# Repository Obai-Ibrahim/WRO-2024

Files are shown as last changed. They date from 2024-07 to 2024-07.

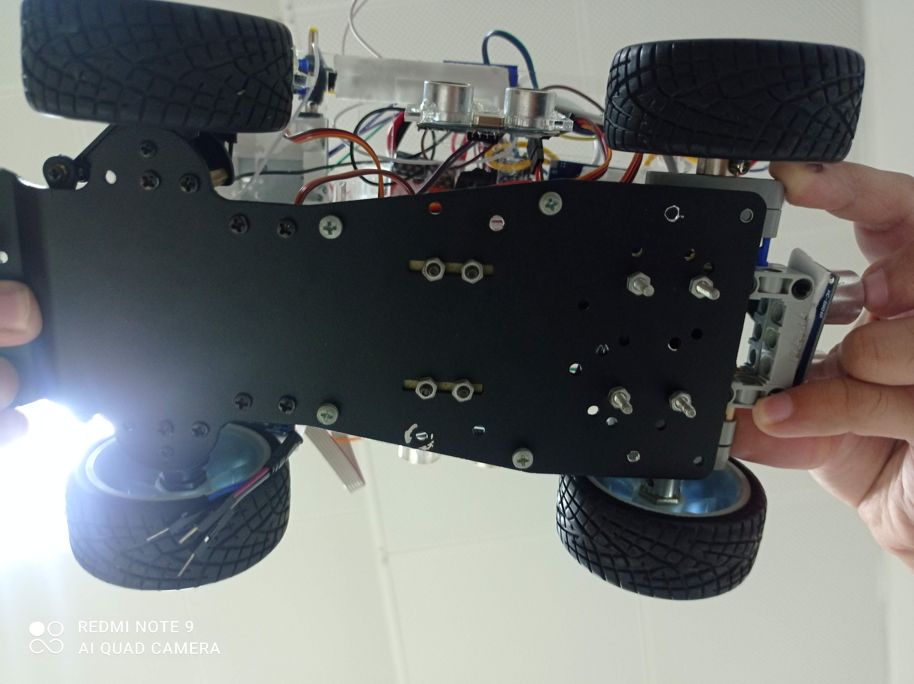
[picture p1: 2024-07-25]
Vehicle Pictures/Bottom.jpg

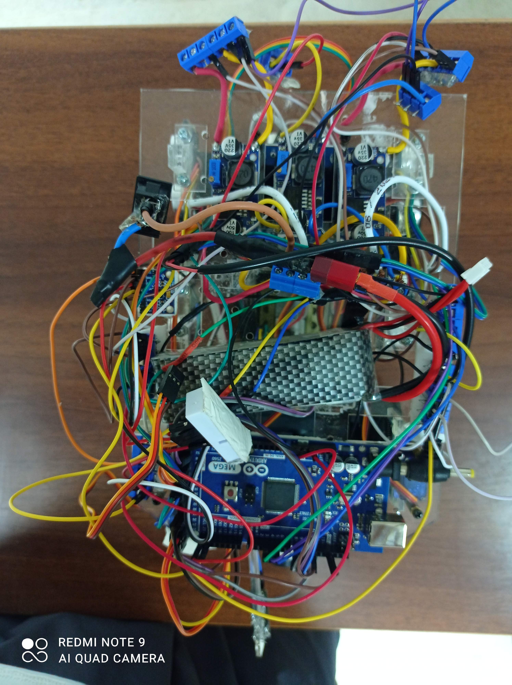
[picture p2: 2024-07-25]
Vehicle Pictures/Up.jpg

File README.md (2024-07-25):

## INTRODUCTION
This Repository contains all the necessary information to build a self-driving car, which can complete three laps and handle different configurations of obstacles.
The code is written with Arduino C programming language, which controls the motor's movement based on the different sensors reading and mainly the information from the pixy cam.
The Repository contains an explanation of many aspects like the strategies and the power and mobility management. In the directory (other) many files will declare the calculation and the algorithms in a better way.
These files are:
Diagrams, DC motor, Power consumption and power supply, Driver.

## Open challenge strategy
For the open challenge, our algorithm depends basically on the distance sensors (HC-SR04) and the IMU (MPU6050) sensor, we implemented a Kalman filter to get accurate measurements of the orientation.
There are 8 ultrasonic sensors postured as shown in (found in others directory).
* The front one is (0) and the back one is (4)
* (2) and  (3) are the right sensors used to detect the turn in the clockwise round.
* (2) and  (3) are the right sensors used to detect the turn in the clockwise round.
* (1)  And (7) are installed on two sgSG-90ervo motors which move according to the Robot’s angle to guarantee good measurement of the perpendicular distance from the walls.
As the new rule states that the vehicle must not touch the outer wall, we declared a dangerous area which is 8cm from the outer wall.
The robot moves forward controlling the direction with PDthe  controller based on MPthe U6050 reading.
## Obstacle challenge strategy
We found out that planning a path for each stretch of the map and guiding the robot to follow it can be a confusing method because it needs perfect calibration for our camera and this may take a long time (maybe preparation time before the round is not sufficient).
So the algorithm in the first turn (the pillars are not known yet) will be: 
The vehicle will pass the forward section in two stages and the corner section in one stage. In the forward section, the pixy will detect the pillars location and then path the pillars one by one (the flow chart in (the others directory will declare this better))

After the first round the pillars positions are known, so we will follow the second strategy:
 By knowing the current position, current heading, target position, and target heading we can generate a polynomial to fit these parameters. Using multiple target points, we create a target path for the robot to follow, steering it towards the next point. This path accounts for the position of obstacles, mapping points to avoid them. We repeat this process until all three rounds are completed.

Note: detailed diagrams for both open and obstacle challenges are included in the directory (others)

## Mobility management
Vehicle’s chassis:
We bought a simple chassis with Ackerman for front-wheel servo steering. The kit contained four wheels, one metal base, nuts and bolts, a DC Motor, and a servo motor with an Ackerman mechanism with no sensors or additional parts. After that, we chose a suitable set of sensors and power supplies. We planned in advance to use a multi-floor design with 3D printed Ultrasonic holders and laser cut floor to have a balanced weight distribution.  
We used another DC motor because the one with the kit was not good, also we changed the rear axle and assembled the wheels with a Lego differential to move better, especially on turns.
To do this we printed a 3D coupler to transfer movement from the engine to the differential’s axis.
The 3D printed parts and plexi laser cut parts are included in the directory (models).
Details of the motor and the torque calculation are in the directory (others).

## Power and sense management
The power calculations are detailed in a PDF file in the directory (scheme). The file contains an accurate calculation of the needed current and the needed supply voltage for the circuit components, in addition, some requirements were considered to choose a suitable battery to supply the sensors and actuators with sufficient power.
The used sensors are: 
1. ultrasonic sensors: dealing with walls and barriers can be enhanced with Ultrasonic Sensor. You shoot out a sound, wait to hear it echo back, and if you have your timing right, you will know how far away the wall is. Using the HC-SR04 Ultrasonic Sensor made it easy for our vehicle to avoid hitting the walls and find its best route between the colored pillars.

2. Gyroscope and accelerometer: We used MPU6050 to determine the vehicle’s rotation angle when it turns right or left. It also helps us to measure acceleration, velocity, orientation, displacement, and many other motion-related parameters of a system or object. This module also has a Digital Motion Processor inside it which is powerful enough to perform complex calculations and thus free up the work for Microcontroller. It has well documented and revised libraries available hence it’s very easy to use with famous platforms like Arduino.

3. TCRT5000Analog: helps to detect the turn if there is doubt with it as it can detect whether the color is white or nonotit is not used so much but can be useful in some cases, it is mounted with a servo motor to control its angle and to put it up when not used so it will not affect the camera readings.

4. Pixy2.1 camera: Using the second version of Pixy made the process smooth and fast with easy-to-detect errors and precise color detection. We faced many problems at the beginning as the camera could only deal with a small range of colors with almost perfect lighting conditions, but this problem was resolved by adjusting camera settings and calibrating it with more than one shade of each color. The information returned by the pixy are the detected objects with their coordinates and sizes.

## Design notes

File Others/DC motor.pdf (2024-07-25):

Torque calculations:

Each DC motor must be capable of generating a torque proportional to the load requirements of the mobile robot. The torque can be calculated using the following formula:

Ffriction = µ ∗ N | (1)

µ: coefficient of friction. N: normal force (Reaction).

N = m ∗ g | (2)

m: robot mass with payload. g: gravitational acceleration.

Facceleration = m ∗ a | (3)

a: robot acceleration.

The total force required for the robot to move:

Ftotal = Ffriction + Facceleration | (4)

T =

Ftotal ∗ r
k

(5)

k: number of DC motors (one motor in our case).

The nominal torque and velocity were

The minimum nominal torque is 8.5 kg. cm and the nominal velocity equals 245 rpm.

Our DC motor
The chosen motor is a 12 volts 350 RPM dc motor (with encoder) with the following specifications:
- Nominal Voltage: 12V
- Gear Reduction Ratio: 34:1
- No Load Speed: 350 rpm
- No Load Current: 20 mA
- Maximum efficiency point parameters: 2.0kg.cm/285rpm/5.0W/0.65A
- Maximum power point parameters: 5.8kg.cm/180rpm/9.0W/1.65A
- Stop current: 5.5A
- Stall torque: 12kg.cm
- Hall Resolution: 374
- Weight: 98g

We chose this dc motor because it has high torque and good speed control, we need this torque especially in starting the motion and in heavy turns as it needs high torque.

The torque helps to maintain a constant speed under in the existence of external loads so it is perfect for this application, also it has a good accurate encoder with 374 pulse per rotation which help to control the velocity and to measure the distance depending on wheel odometry.

Additionally, this motor can be easily controlled by a motor driver (which is BTS 7960 in our case), this make it suitable for robotics applications that requires precise motion.

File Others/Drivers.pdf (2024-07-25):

Drivers: BTS9670:

BTS7960 Motor Driver:

We used BTS7960 motor driver to control the speed and direction of the

DC motor. It is widely used with robotics, consumer electronics, automation

and other projects. It has very low voltage drop compared to other drivers

like L298N

Technical Specifications:

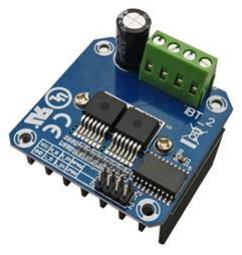
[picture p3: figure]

- Input Voltage: 6 – 27 V
- Driver: Dual BTS7960 H Bridge Configuration.
- Peak current: 43 A
- PWM capability of up to 25 kHz
- Control Input Level: 3.3 – 5V
- Control Mode: PWM or level
- Board Size (LxWxH): 50mm x 50mm x 43mm
- Weight: ~66g

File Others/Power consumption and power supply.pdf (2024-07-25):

Power consumption and power supply:

The following table contains each motor/sensor nominal current and supply (input) voltage:

Sensor/Motor/controller | Number of pieces | Nominal current(mA) | Total (mA) | Supply (input) voltage(volts)
Arduino mega | 1 | 74 | 74 | 8
BTS 7960 | 1 | 10 | 10 | 12(for motor) and 5 (for the inner controller)
Voltage regulator | 3 | 8 | 8 | 12
Pixy cam | 1 | 140 | 140 | 5
HC-SR04 sensor | 8 | 21 | 161 | 5
MPU6050 | 1 | 10 | 10 | 3.3
Motor Encoder | 1 | 2 | 2 | 5
TCRT5000 ANALOG | 1 | 7 | 7 | 5
MG995 servo motor | 1 | 350 | 350 | 5.8
SG-90 servo motor | 3 | 270 | 810 | 4.8
DC motor | 1 | 1650 | 1650 | 12 (BTS output)

The maximum needed input voltage is 12 volts
And the consumed current is 3.222 Amp if all the electronic components and actuator work simultaneously.

To choose our power supply we need to consider the following requirements:

- Stable current output
- High voltage under load
- Low temperature under high discharge
- Good capacity (can run the robot for 30 minutes at least)
- Low weight

To run the robot for 0.5 hour under a discharge of 3.2A we need minimum capacity of 1600 Ma Considering the previous requirements, we choose an 1800 11.1v 1.8Ah Li-Po battery.

Li-poly Battery:

We used one Li-poly battery to supply the Arduino board, sensors, DC and servo Motors and BTS.

Technical specifications:

Voltage: +11.1V

Capacity: 4200mAh

Number of cells: 3 cells

Weight: 315g

Size: 139mm x 43mm x 25mm

Plug: XT60 black

Charging connector: JST-XHR white

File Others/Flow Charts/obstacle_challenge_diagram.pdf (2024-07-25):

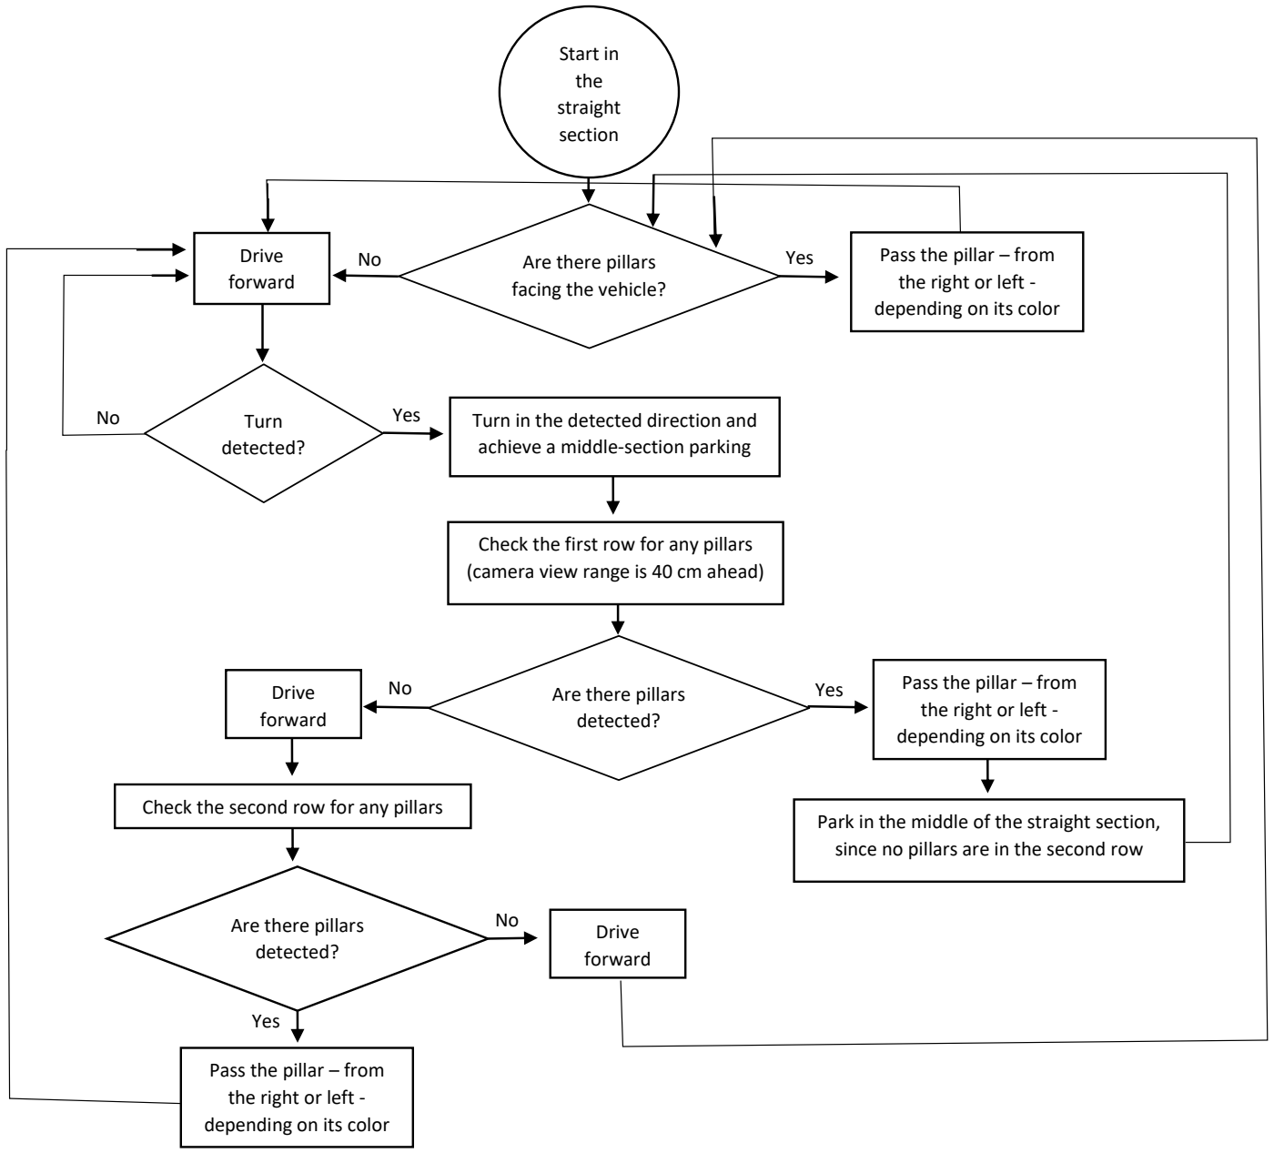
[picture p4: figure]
Start in the straight section; Are there pillars facing the vehicle?; Drive; Yes; forward; Turn detected?; achieve a middle-section parking; Pass the pillar – from the right or left - depending on its color; Check the first row for any pillars (camera view range is 40 cm ahead); Are there pillars detected?; Pass the pillar – from; the right or left - depending on its color; since no pillars are in the second row; Drive forward; Check the second row for any pillars

No | Yes | Turn in the detected direction and

Park in the middle of the straight section,

Note:

Regarding the parking lot, we considered passing next to it when it is not the final lap yet.

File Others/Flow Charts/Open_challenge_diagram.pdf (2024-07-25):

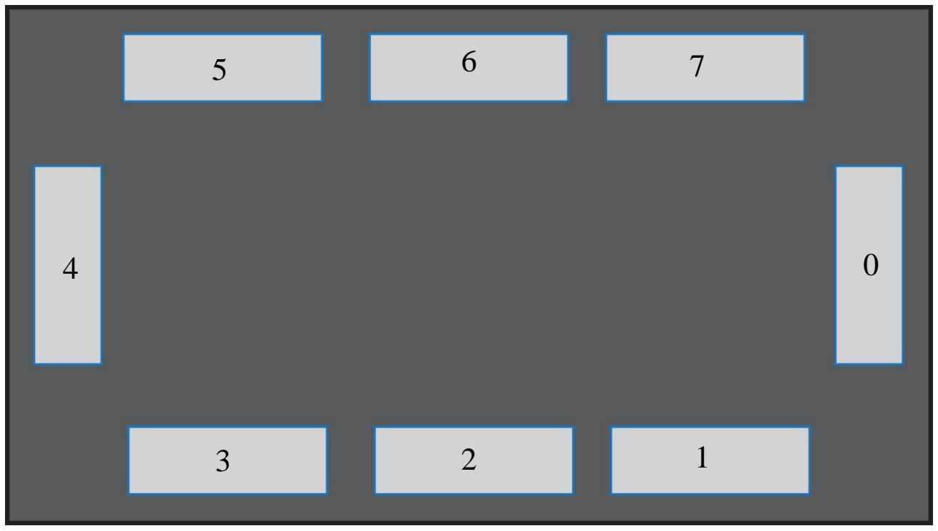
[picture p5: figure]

Sensor ID | Name | Sensor ID | Name
0 | Front | 4 | Back
1 | Right Servo | 5 | Back left
2 | Middle right | 6 | Middle left
3 | Back right | 7 | Left Servo

“Right Servo” and “Left Servo” are ultrasonic sensors put on two servomotors on the right and left respectively.

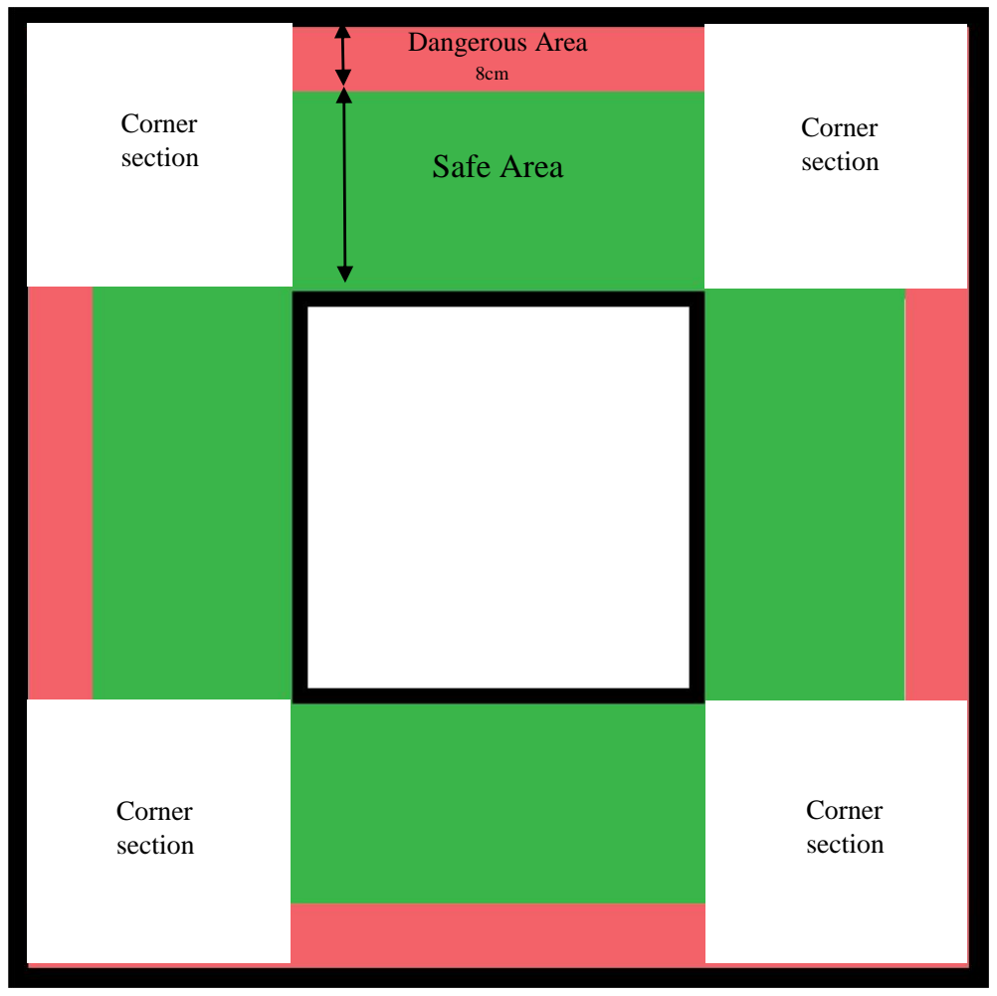
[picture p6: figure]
Safe Area; Dangerous Area; Corner section
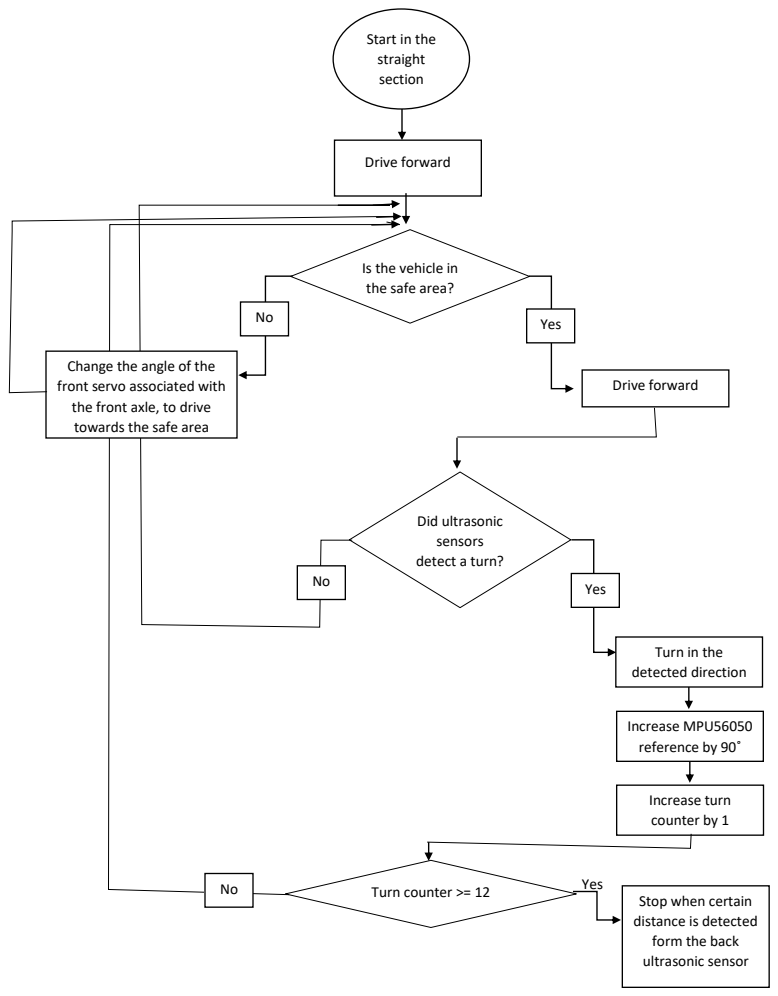
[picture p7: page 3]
Drive forward; Yes No; Did ultrasonic sensors detect a turn? Yes No; Increase MPU56050 reference by 90˚; Increase turn counter by 1; Turn counter >= 12; Yes

Start in the
straight
section

Is the vehicle in
the safe area?

Change the angle of the
front servo associated with
the front axle, to drive
towards the safe area

Turn in the
detected direction

Stop when certain
distance is detected
form the back
ultrasonic sensor

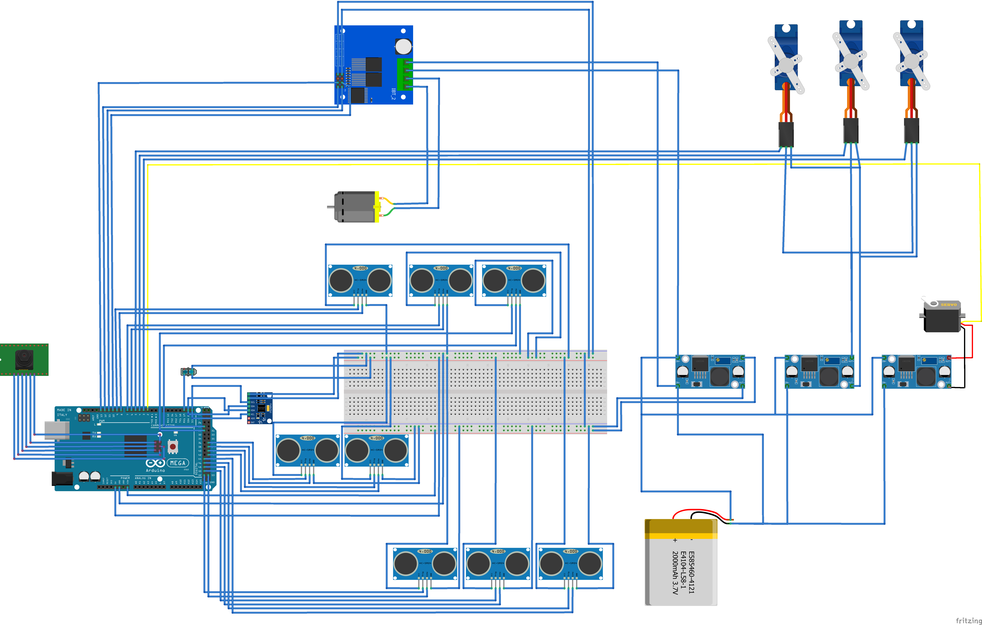
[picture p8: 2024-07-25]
Scheme/WRO_bb.png

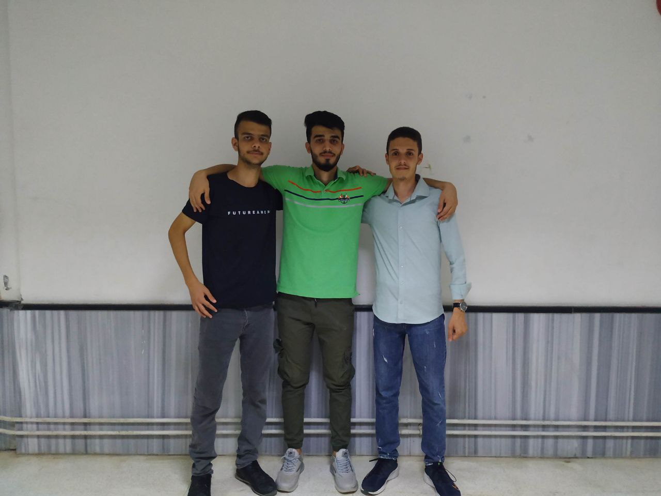
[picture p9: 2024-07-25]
Team Photos/Official.jpg

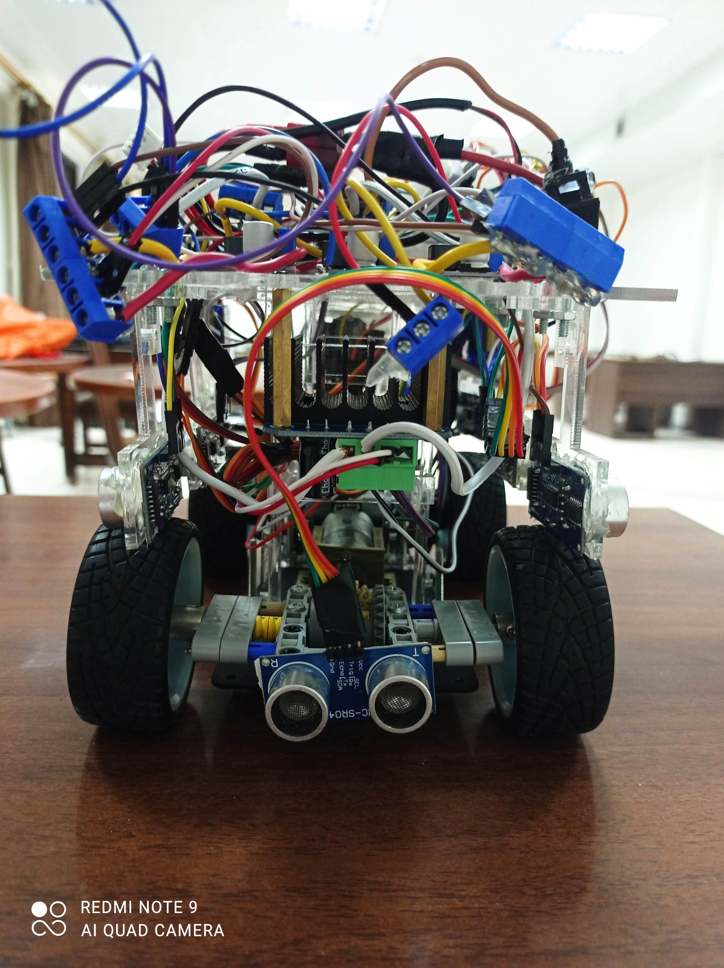
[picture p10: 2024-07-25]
Vehicle Pictures/Back.jpg

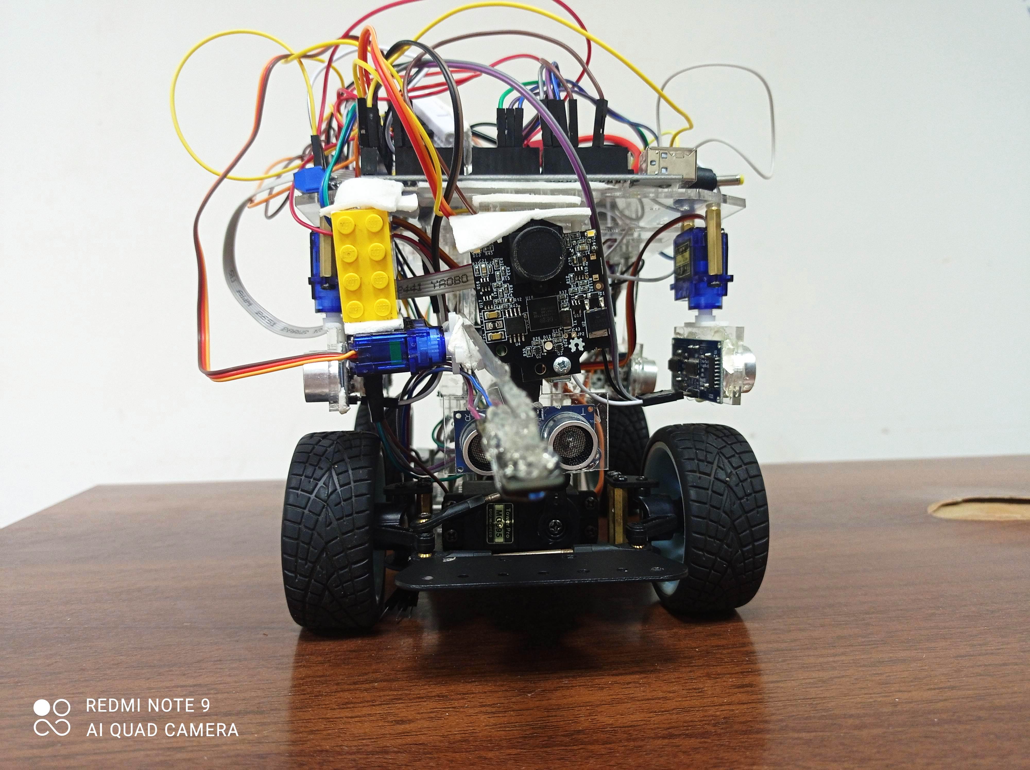
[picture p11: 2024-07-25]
Vehicle Pictures/Front.jpg

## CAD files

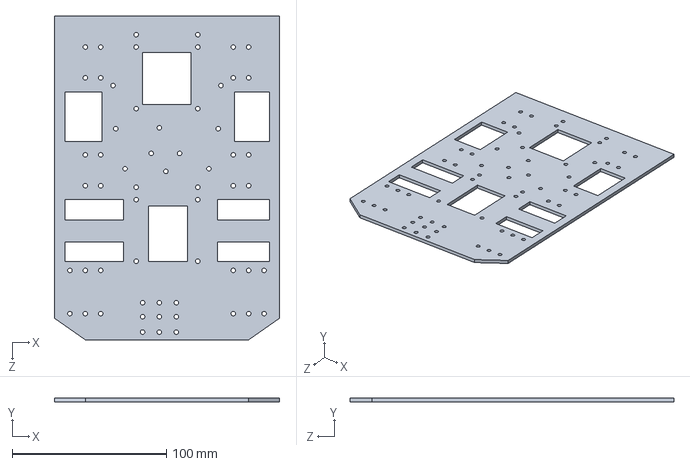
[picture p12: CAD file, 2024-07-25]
Model/Plexi/MAIN.SLDPRT
146.0 x 2.54 x 210.0 mm

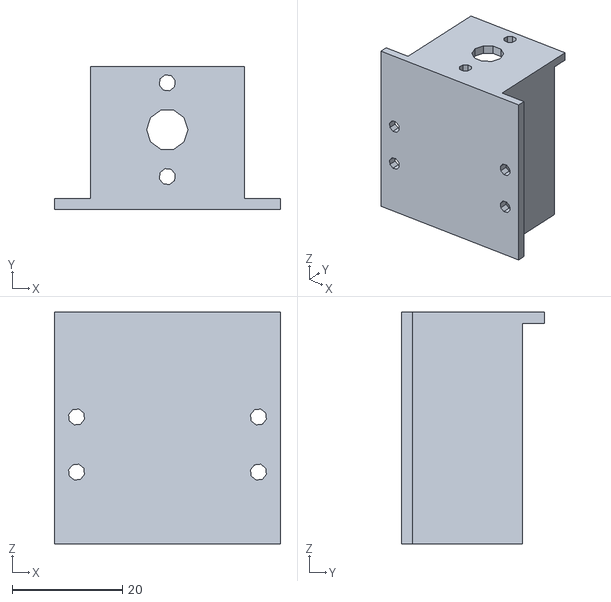
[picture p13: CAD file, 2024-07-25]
Model/3D Print/Dc_motor_holderstl.stl
41.0 x 26.0 x 42.0

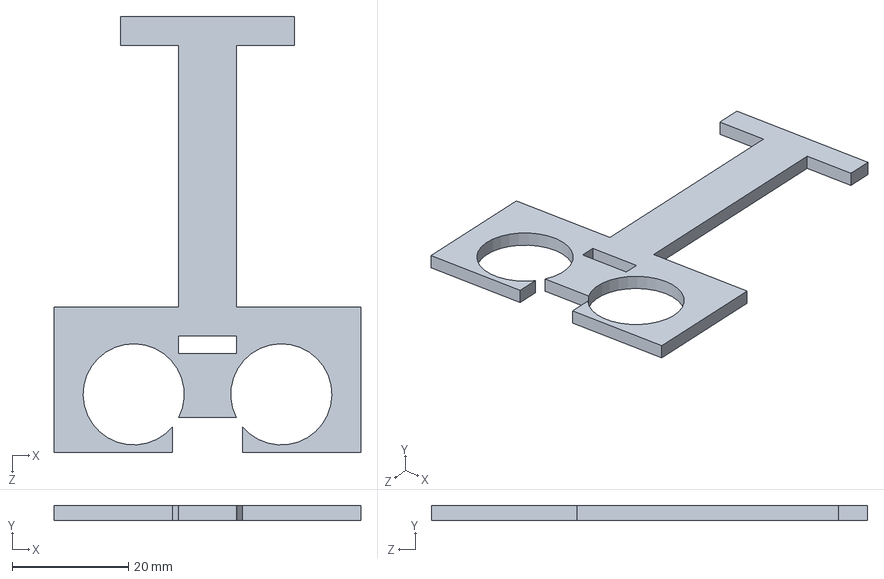
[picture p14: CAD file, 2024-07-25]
Model/Plexi/Ultrasonic holder.SLDPRT
52.8 x 2.54 x 75.0 mm

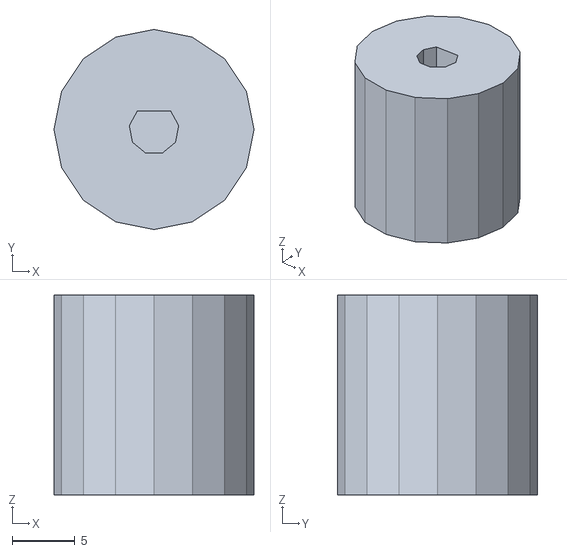
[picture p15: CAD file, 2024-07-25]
Model/3D Print/coupler.stl
16.0 x 16.0 x 16.0

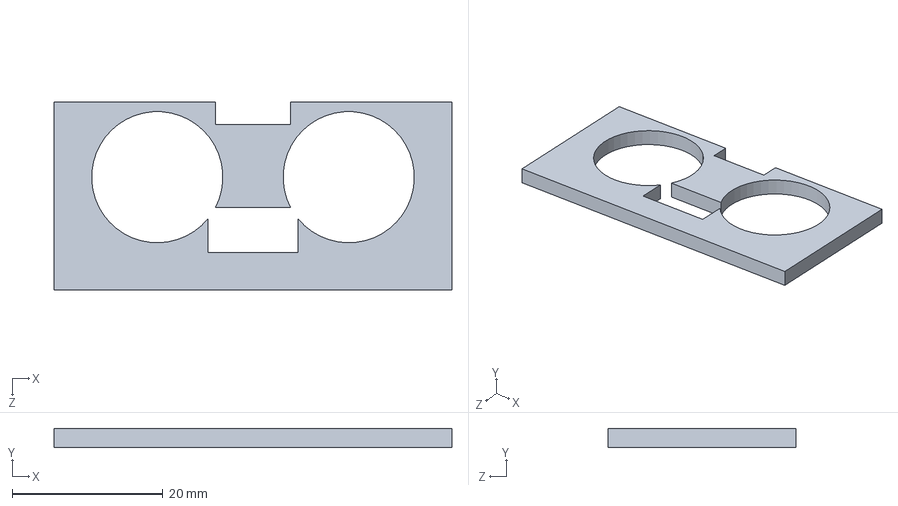
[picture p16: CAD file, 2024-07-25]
Model/Plexi/Ultrasonic servo holder.SLDPRT
52.8 x 2.54 x 25.0 mm

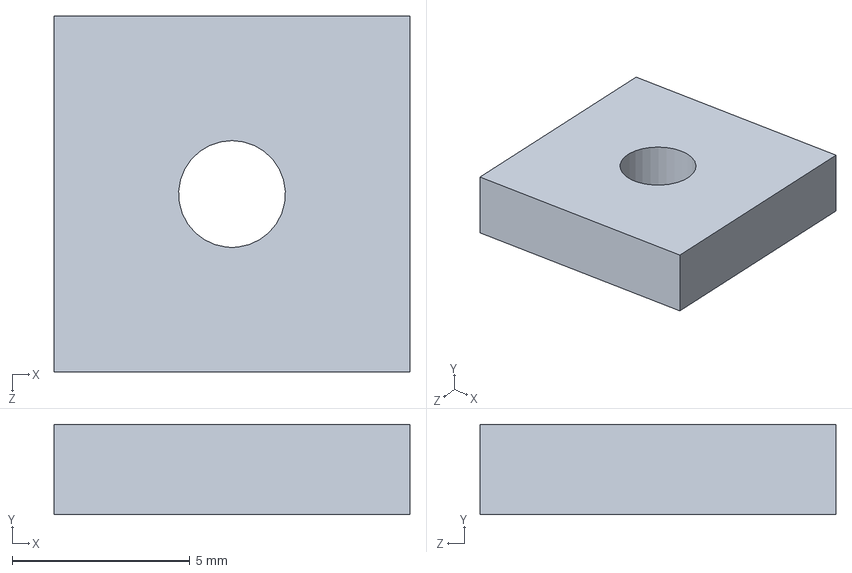
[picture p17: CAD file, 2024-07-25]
Model/Plexi/Mount 2.SLDPRT
10.0 x 2.54 x 10.0 mm

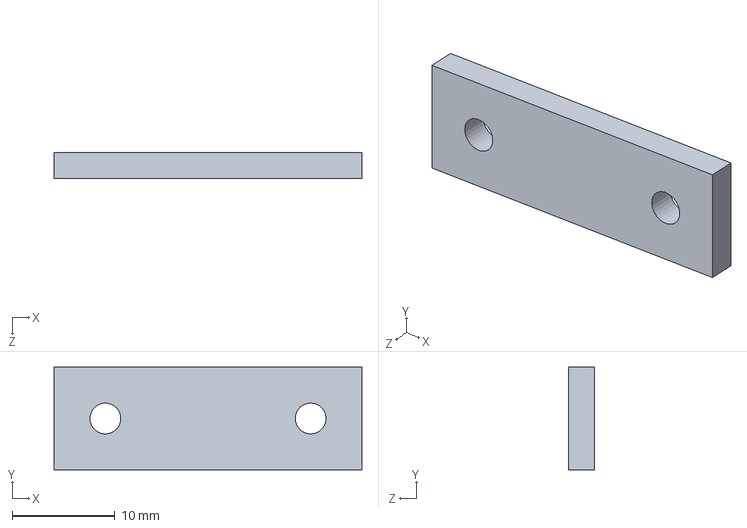
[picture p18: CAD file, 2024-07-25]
Model/Plexi/Mount 1.SLDPRT
30.0 x 10.0 x 2.54 mm

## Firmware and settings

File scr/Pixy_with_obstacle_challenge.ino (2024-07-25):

#include <Servo.h>
#include <NewPing.h>
#include <Pixy2.h>
#include <ArduinoQueue.h>
#include "impu.h"
long t;
int x = 0;
long time_delay;
// MPU6050 module values
int number_of_turns = 0;
float yaw, last_yaw = 0;
double delta_yaw, real_value = 0;
double imu_overall_val = 0;         //yaw overall value from the starting position range from -360 * 3 to 360 * 3
double imu_current_val = 0;         //yaw straight section value range from -90 to 90
int mx = 41, my = 20, mz = -2;              //imu mpu6050 offsets used for calibration
impu imu(mx, my);

// enc
volatile byte reading = 0;
static int A_R = 2 ;
volatile int aFlag_R = 0;
static int B_R = 3;
volatile int bFlag_R = 0;
int Pos_R = 0;
// enc

Pixy2 p;
double m = 0.0185;
int left_g = A2, left_y = A3, right_g = A0, right_y = A1;
int Servo_Pin = 3;
int ServoStraight = 105;
int Servo_Left_Range = 40;
int Servo_Right_Range = 40;
int ServoCritical_Left_Range = 60;
int ServoCritical_Right_Range = 35;
double duration_R1, duration_R2, duration_L1, duration_L2, duration_F, duration_B, duration_SL, duration_SR, f, b, fl, fr, bl, br, sr, sl  , Real_left = 0, Real_right = 0;
double front = 0, back = 0, right1 = 0, right2 = 0, left1 = 0, left2 = 0, servo_left = 0, servo_right = 0;
int front_id = 0, servor_id = 7, right1_id = 2, right2_id = 3, back_id = 4, left2_id = 5, left1_id = 6, servol_id = 7;
int echo[9] = { 26 , 30 , 42 , 44 , 46 , 50 , 52 , 22  };
int trig[9] = { 27 , 31 , 43 , 45 , 47 , 51 , 53 , 23 };
int Filter_Size = 7;
int threshold = 13;
double temp = 0;
double mean_bl = 0;
ArduinoQueue <double> Means_BL;
double mean_fl = 0;
ArduinoQueue <double> Means_FL;
double mean_br = 0;
ArduinoQueue <double> Means_BR;
double mean_fr = 0;
ArduinoQueue <double> Means_FR;
double mean_f = 0;
ArduinoQueue <double> Means_F;
double mean_b = 0;
ArduinoQueue<double> Means_B;
double mean_sl = 0;
ArduinoQueue <double> Means_SL;
double mean_sr = 0;
ArduinoQueue <double> Means_SR;
int MAX_DISTANCE = 300;


NewPing ultra[8] = {     // Sensor object array.
  NewPing(trig[0], echo[0], MAX_DISTANCE),
  NewPing(trig[1], echo[1], MAX_DISTANCE),
  NewPing(trig[2], echo[2], MAX_DISTANCE),
  NewPing(trig[3], echo[3], MAX_DISTANCE),
  NewPing(trig[4], echo[4], MAX_DISTANCE),
  NewPing(trig[5], echo[5], MAX_DISTANCE),
  NewPing(trig[6], echo[6], MAX_DISTANCE),
  NewPing(trig[7], echo[7], MAX_DISTANCE)
};
int MPU = 0;
int mpu_reference = 0;
double mpu_kp = 3, mpu_kd = 1.5, mpu_error, mpu_prev_error, mpu_time, mpu_last_time, ultra_error, ultra_kpL = 2.5, ultra_kpR = 4;

long t1;
int R_EN = 11;
int L_EN = 10;
int R_PWM = 9;
int L_PWM = 8;
Servo A;
Servo R;
Servo L;
int thresh = 90;
int deg = 87;

double ang, distance;
int left_turn = 0, right_turn = 0, turn_counter = 0;
int turn_range = 40;
int speed_turn_back = 30, speed_turn = 30, speed_befor_turn = 20, speed_normal = 30, speed_danger = 15;




double Filter(double read, double &last_mean, ArduinoQueue <double> &Means)
{
  if (Means.isEmpty())
  {
    last_mean = read;
    for (int i = 0; i < Filter_Size; i++)
    {
      Means.enqueue(read);
    }
  }
  else
  {
    temp = Means.dequeue();
    last_mean -= (double(temp / Filter_Size));
    last_mean += (double(read / Filter_Size));
    Means.enqueue(read);
  }
  return last_mean;
}

double get_distance_F()
{
  duration_F = ultra[0].ping();
  f = (duration_F / 2) * 0.0343;// Calculate the distance based on utlra sonic wave speed and time taken by the wave.
  if (f == 0)
    f = MAX_DISTANCE;
  mean_f = Filter(f, mean_f, Means_F);// Take the filtered value
  return mean_f;
}

double get_distance_B() {
  duration_B = ultra[4].ping();
  b = ((duration_B / 2) * 0.0343);
  if (b == 0)
    b = MAX_DISTANCE;
  mean_b = Filter(b, mean_b, Means_B);
  return mean_b;
}

double get_distance_SL ()
{
  duration_SL = ultra[7].ping();
  sl = (duration_SL / 2) * 0.0343;// Calculate the distance based on utlra sonic wave speed and time taken by the wave.
  if (sl == 0)
    sl = MAX_DISTANCE;
  mean_sl = Filter(sl, mean_sl, Means_SL);// Take the filtered value
  return mean_sl;
}

double get_distance_SR ()
{
  duration_SR = ultra[1].ping();
  sr = (duration_SR / 2) * 0.0343;// Calculate the distance based on utlra sonic wave speed and time taken by the wave.
  if (sr == 0)
    sr = MAX_DISTANCE;
  mean_sr = Filter(sr, mean_sr, Means_SR);// Take the filtered value
  return mean_sr;
}

double get_distance_L1 ()
{
  duration_L1 = ultra[6].ping();
  fl = ((duration_L1 / 2) * 0.0343)  ;
  if (fl == 0)
    fl = MAX_DISTANCE;
  mean_fl = Filter(fl, mean_fl, Means_FL);
  return mean_fl ;
}

double get_distance_L2()
{
  duration_L2 = ultra[5].ping();
  bl = ((duration_L2 / 2) * 0.0343)  ;
  if (bl == 0)
    bl = MAX_DISTANCE;
  mean_bl = Filter(bl, mean_bl, Means_BL);
  return mean_bl;
}

double get_distance_R1 ()
{
  duration_R1 = ultra[2].ping();
  fr = ((duration_R1 / 2) * 0.0343);
  if (fr == 0)
    fr = MAX_DISTANCE;
  mean_fr = Filter(fr, mean_fr, Means_FR);
  return mean_fr;
}

double get_distance_R2()
{
  duration_R2 = ultra[3].ping();
  br = ((duration_R2 / 2) * 0.0343) ;
  if (br == 0)
    br = MAX_DISTANCE;
  mean_br = Filter(br, mean_br, Means_BR);

  return mean_br ;
}


void reset_means()
{
  for (int i = 0 ; i < Filter_Size ; i++)
  {
    Means_B.dequeue();
    Means_BL.dequeue();
    Means_BR.dequeue();
    Means_FL.dequeue();
    Means_FR.dequeue();
    Means_F.dequeue();
    Means_SL.dequeue();
    Means_SR.dequeue();
  }
}

double Real_distance(double read_1, double read_2) {
  return (read_1 + read_2) / 2 * cos((yaw - mpu_reference) * PI / 180);
}

double Fast_dist(int id) {
  double duration = ultra[id].ping();
  double fast_distance = ((duration / 2) * 0.0343);
  if (fast_distance == 0)
    fast_distance = MAX_DISTANCE;
  return fast_distance;
}


void my_delay(int t) {
  time_delay = millis();
  while (millis() - time_delay < t)
  {
    read_yaw();
  }
}

void update_sensors()
{
  front = get_distance_F();
  my_delay(10);
  back = get_distance_B();
  my_delay(10);
  left1 = get_distance_L1();
  my_delay(10);
  right1 = get_distance_R1();
  my_delay(10);
  left2 = get_distance_L2();
  my_delay(10);
  right2 = get_distance_R2();
  my_delay(10);
  servo_right = get_distance_SR();
  my_delay(10);
  servo_left = get_distance_SL();
  //Real_left = Real_distance(left1, left2);
  //Real_right = Real_distance(right1, right2);
}


void Motor_forward(int percent) {
  int PWM = percent * 254 / 100;
  analogWrite(R_PWM, PWM);
  analogWrite(L_PWM, 0);
}


void Motor_backward(int percent) {
  int PWM = percent * 254 / 100;
  analogWrite(L_PWM, PWM);
  analogWrite(R_PWM, 0);
}


void Motor_stop() {
  analogWrite(R_PWM, 0);
  analogWrite(L_PWM, 0);
}



void Ser(int deg) {
  if (deg < ServoStraight - Servo_Left_Range)
    A.write(ServoStraight - Servo_Left_Range);
  else if (deg > ServoStraight + Servo_Right_Range)
    A.write(ServoStraight + Servo_Right_Range);
  else
    A.write(deg);
}

void Ser_Critical(int deg) {
  if (deg < ServoStraight - ServoCritical_Left_Range)
    A.write(ServoStraight - ServoCritical_Left_Range);
  else if (deg > ServoStraight + ServoCritical_Right_Range)
    A.write(ServoStraight + ServoCritical_Right_Range);
  else
    A.write(deg);
  delay(50);
}



void Back_MPU_pid() {
  mpu_error = imu_current_val - mpu_reference;
  Ser(ServoStraight + (mpu_kp * mpu_error));
}

void Front_MPU_pid() {
  mpu_error = imu_current_val - mpu_reference;
  Ser(ServoStraight - (mpu_kp * mpu_error));
}


void servo_ultra_pid() {
  double error = imu_current_val - mpu_reference;
  delay(10);
  if (error > 80) {
    L.write(10);
    R.write(10);
  }
  else if (error < -80) {
    L.write(170);
    R.write(170);
  }
  else {
    L.write(90 - error);
    R.write(90 - error);
  }
  //  mpu.update();
}



void setup() {
  //Serial.begin(115200);
  imu.init();
  Wire.setWireTimeout(3000, true);
  Serial.begin(9600);
  p.init();
  delay(30);
  Serial.println("Ok");
  pinMode(L_EN, OUTPUT);
  pinMode(R_EN, OUTPUT);
  pinMode(R_PWM, OUTPUT);
  pinMode(L_PWM, OUTPUT);
  //Serial.println("hello");

  /*   pinMode(A0, OUTPUT);
     pinMode(A1, OUTPUT);
     pinMode(A2, OUTPUT);
     pinMode(A3, OUTPUT);
     pinMode(A7, INPUT);*/
  //setup motors states


  //enc
  //  attachInterrupt(0, PinA_R, RISING);
  // pinMode(A_R, INPUT);
  // attachInterrupt(1, PinB_R, RISING);
  // pinMode(B_R, INPUT);
  //enc
  digitalWrite(L_EN, HIGH);
  digitalWrite(R_EN, HIGH);
  A.attach(3);
  R.attach(5);
  L.attach(4);
  A.write(ServoStraight);
  R.write(90);
  L.write(90);
  //analogWrite(R_PWM, 0);
  //analogWrite(L_PWM, 0);
  delay(500);
  //delay(500);
  //Serial.println("hello");
  //mpu_reference = mpu.getAngleZ();
  read_yaw();
  mpu_reference = yaw;
}



void Turn_right() {
  L.write(90);
  reset_means();
  while (get_distance_F() > 60)
  {
    my_delay(30);
    if (Fast_dist(7) > 65)
      A.write(ServoStraight - 5);
    else
      Front_MPU_pid();
    update_sensors();
    Motor_forward(40);
    read_yaw();
  }
  Motor_stop();
  my_delay(100);
  while ( ( Fast_dist(2) < 25 || Fast_dist(3) < 25 ) && ( Fast_dist(5) < 35 || Fast_dist(6) < 35) )
  {
    A.write(ServoStraight - 5 );
    Motor_forward(40);
    read_yaw();
    update_sensors();
  }
  Motor_stop();
  A.write(ServoStraight);
  my_delay(100);
  
  
  double d=get_distance_SL();
  if (d < 25)
  {
    while (get_distance_F() < 67)
    { Motor_backward(40);
      Back_MPU_pid();
      my_delay(30);
    }
    Motor_stop();
    A.write(ServoStraight + 35);
    R.write(20);
    L.write(160);
    read_yaw();
    reset_means();
    my_delay(100);
    Motor_forward(40);

    while (imu_current_val < mpu_reference + 90)
    { my_delay(30);
      if (Fast_dist(0) < 20 || Fast_dist(1) < 20 || Fast_dist(7) < 20)
        break;
    }
    mpu_reference += 90;
    Motor_stop();
    A.write(ServoStraight);
    R.write(90);
    L.write(90);
    my_delay(50);
    while (Fast_dist(4) > 20)
    { my_delay(30);
      Motor_backward(40);
      Back_MPU_pid();
    }
    while (Fast_dist(4) < 20)
    { my_delay(30);
      Motor_forward(40);
      Front_MPU_pid();
    }
    Motor_stop();
    A.write(ServoStraight);
    my_delay(100);
  }


  else if (d < 45)
    {
    while (Fast_dist(0) < 65)
    { Motor_backward(40);
      Back_MPU_pid();
      my_delay(30);
    }
    while ( get_distance_SL() > 25)
    {
      A.write(ServoStraight - 35);
      Motor_forward(40);
      servo_ultra_pid();
      my_delay(30);
    }
    Motor_stop();
    A.write(ServoStraight + 35);
    L.write(90);
    R.write(10);
    my_delay(100);
    Motor_forward(40);
    while (imu_current_val < mpu_reference)
    {
      my_delay(30);
      if (Fast_dist(0) < 15 || Fast_dist(1) < 15)
        break;
    }
    
    Motor_stop();
    R.write(90);
    A.write(ServoStraight);
    my_delay(50);

    while (get_distance_F() < 67)
    { Motor_backward(40);
      Back_MPU_pid();
      my_delay(30);
    }

    Motor_stop();
    A.write(ServoStraight + 35);
    R.write(20);
    L.write(160);
    read_yaw();
    reset_means();
    my_delay(100);
    Motor_forward(40);

    while (imu_current_val < mpu_reference + 90)
    { my_delay(30);
      if (Fast_dist(0) < 20 || Fast_dist(1) < 20 || Fast_dist(7) < 20)
        break;
    }
    mpu_reference += 90;
    Motor_stop();
    A.write(ServoStraight);
    R.write(90);
    L.write(90);
    my_delay(50);
    while (Fast_dist(4) > 20)
    { my_delay(30);
      Motor_backward(40);
      Back_MPU_pid();
    }
    while (Fast_dist(4) < 20)
    { my_delay(30);
      Motor_forward(40);
      Front_MPU_pid();
    }
    Motor_stop();
    A.write(ServoStraight);
    my_delay(100);
    }

    
    else
    {
    if (Fast_dist(7) > 70)
    {
      while (Fast_dist(0) > 30)
      {
        Motor_forward(40);
        A.write(ServoStraight-5);
        my_delay(30);
      }
    }
    else {
      while (Fast_dist(0) > 30)
      {
        Motor_forward(40);
        Front_MPU_pid();
        my_delay(30);
      }
    }
    Motor_stop();
    A.write(ServoStraight+25);
    my_delay(100);
    while (Fast_dist(0) > 15)
      {
        Motor_forward(40);
        my_delay(30);
      }

    Motor_stop();
    A.write(ServoStraight - 55);
    my_delay(100);
    while (imu_current_val < mpu_reference + 83)
    { Motor_backward(40);
    my_delay(30);
      if (Fast_dist(4) < 15)
        break;
    }
    Motor_stop();
    A.write(ServoStraight);
    my_delay(50);
    mpu_reference+=90;
    while (Fast_dist(4) > 20)
    { my_delay(30);
      Motor_backward(40);
      Back_MPU_pid();
    }
    while (Fast_dist(4) < 20)
    { my_delay(30);
      Motor_forward(40);
      Front_MPU_pid();
    }
    Motor_stop();
    A.write(ServoStraight);
    my_delay(100);
    }
  reset_means();
}






void Turn_left() {
  R.write(90);
  reset_means();
  while (get_distance_F() > 60) //to read the correct distance from the wall 
  {
    my_delay(30);
    if (Fast_dist(1) > 65)
      A.write(ServoStraight + 5);
    else
      Front_MPU_pid();
    update_sensors();
    Motor_forward(40);
    read_yaw();
  }
  Motor_stop();
  my_delay(100);
  while ( ( Fast_dist(2) < 35 || Fast_dist(3) < 35 ) && ( Fast_dist(5) < 25 || Fast_dist(6) < 25) )
  {
    A.write(ServoStraight+5 );
    Motor_forward(40);
    read_yaw();
    update_sensors();
  }
  Motor_stop();
  A.write(ServoStraight);
  my_delay(100);


  double d=get_distance_SR();
  if (d < 25)
  {
    while (get_distance_F() < 69)
    { Motor_backward(40);
      Back_MPU_pid();
      my_delay(30);
    }
    
    Motor_stop();
    A.write(ServoStraight - 40);
    R.write(20);
    L.write(160);
    read_yaw();
    reset_means();
    my_delay(100);
    Motor_forward(40);

    
    while (imu_current_val > mpu_reference - 90)
    { my_delay(30);
      if (Fast_dist(0) < 20 || Fast_dist(1) < 20 || Fast_dist(7) < 20)
        break;
    }
    mpu_reference -= 90;
    Motor_stop();
    A.write(ServoStraight);
    R.write(90);
    L.write(90);
    my_delay(50);
    while (Fast_dist(4) > 20)
    { my_delay(30);
      Motor_backward(40);
      Back_MPU_pid();
    }
    while (Fast_dist(4) < 20)
    { my_delay(30);
      Motor_forward(40);
      Front_MPU_pid();
    }
    Motor_stop();
    A.write(ServoStraight);
    my_delay(100);
  }

  
  else if (d < 45)
    {
    while (Fast_dist(0) < 65)
    { Motor_backward(40);
      Back_MPU_pid();
      my_delay(30);
    }
    while ( get_distance_SR() > 25)
    {
      A.write(ServoStraight + 35);
      Motor_forward(40);
      servo_ultra_pid();
      my_delay(30);
    }
    Motor_stop();
    A.write(ServoStraight - 40);
    R.write(90);
    L.write(170);
    my_delay(100);
    Motor_forward(40);
    while (imu_current_val > mpu_reference)
    {
      my_delay(30);
      if (Fast_dist(0) < 15 || Fast_dist(7) < 15)
        break;
    }
    
    Motor_stop();
    L.write(90);
    A.write(ServoStraight);
    my_delay(50);
    
    while (get_distance_F() < 69)
    { Motor_backward(40);
      Back_MPU_pid();
      my_delay(30);
    }
    
    Motor_stop();
    A.write(ServoStraight - 40);
    R.write(20);
    L.write(160);
    read_yaw();
    reset_means();
    my_delay(100);
    Motor_forward(40);
    
    while (imu_current_val > mpu_reference - 90)
    { my_delay(30);
      if (Fast_dist(0) < 20 || Fast_dist(1) < 20 || Fast_dist(7) < 20)
        break;
    }
    mpu_reference -= 90;
    Motor_stop();
    A.write(ServoStraight);
    R.write(90);
    L.write(90);
    my_delay(50);
    while (Fast_dist(4) > 20)
    { my_delay(30);
      Motor_backward(40);
      Back_MPU_pid();
    }
    while (Fast_dist(4) < 20)
    { my_delay(30);
      Motor_forward(40);
      Front_MPU_pid();
    }
    Motor_stop();
    A.write(ServoStraight);
    my_delay(100);
  }

  
  else
    {
     if (Fast_dist(1) > 70)
    {
      while (Fast_dist(0) > 30)
      {
        Motor_forward(40);
        A.write(ServoStraight+5);
        my_delay(30);
      }
    }
    else {
      while (Fast_dist(0) > 30)
      {
        Motor_forward(40);
        Front_MPU_pid();
        my_delay(30);
      }
    }
    Motor_stop();
    A.write(ServoStraight-25);
    my_delay(100);
    while (Fast_dist(0) > 15)
      {
        Motor_forward(40);
        my_delay(30);
      }

    Motor_stop();
    A.write(ServoStraight + 40);
    my_delay(100);
    while (imu_current_val > mpu_reference - 83)
    { Motor_backward(40);
    my_delay(30);
      if (Fast_dist(4) < 15)
        break;
    }
    Motor_stop();
    A.write(ServoStraight);
    my_delay(50);
    mpu_reference-=90;
    while (Fast_dist(4) > 20)
    { my_delay(30);
      Motor_backward(40);
     Back_MPU_pid();
    }
    while (Fast_dist(4) < 20)
    { my_delay(30);
      Motor_forward(40);
      Front_MPU_pid();
    }
    Motor_stop();
    A.write(ServoStraight);
    my_delay(100);
    }
  reset_means();
}
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
void loop() {
 if(read_cam()=='g') //pixy cam read green pillar
    startup('g');  //avoid pillar from left side
  else if(read_cam()=='r') //pixy cam read red pillar
    startup('r');  //avoid pillar from right side
  else
  {while(1)
  {Motor_forward(40);
  Front_MPU_pid();
  if(sl>100) //when the servo left ultrasonic read more than 100cm ,the vehicle turns left
    {Turn_left();
    break;}
  if(sr>100) //when the servo right ultrasonic read more than 100cm ,the vehicle turns right
    {Turn_right();
    break;}
  }
}
rest_means();
update_sensors();
if(read_cam()=='g') //pixy cam read green pillar
    startup('g');  //avoid pillar from left side
  else if(read_cam()=='r') //pixy cam read red pillar
    startup('r');  //avoid pillar from right side
  else
  {while(1)
  {Motor_forward(40);
  if(read_cam()!='n')
  break;
  }
}
rest_means();
update_sensors();

if(read_cam()=='g') //pixy cam read green pillar
    startup('g');  //avoid pillar from left side
  else if(read_cam()=='r') //pixy cam read red pillar
    startup('r');  //avoid pillar from right side
  else
  {while(1)
  {Motor_forward(40);
  Front_MPU_pid();
  if(sl>100) //when the servo left ultrasonic read more than 100cm ,the vehicle turns left
    {Turn_left();
    break;}
  if(sr>100) //when the servo right ultrasonic read more than 100cm ,the vehicle turns right
    {Turn_right();
    break;}
  }
}
rest_means();
Motor_stop();
delay(10000);
}




void read_yaw() {
  imu.getyaw(yaw);        //get the value of yaw

  if (Wire.getWireTimeoutFlag()) {
    Wire.end();
    delay(10);
    Wire.begin();
    delay(10);
    Wire.clearWireTimeoutFlag();
  }
  //delay(5);         //so it won't ask the dmp for too many values in a short time
  delta_yaw = yaw - last_yaw ;    //get the delta of yaw value
  if (delta_yaw < 150 && delta_yaw > -150) { //solving the problem that the dmp return values 180 and -180 in a random
    real_value += delta_yaw;
    imu_overall_val = real_value; // kalman.updateEstimate(real_value);
  }
  last_yaw = yaw;
  imu_current_val = imu_overall_val ;//+ 90 * number_of_turns;   // get the yaw straight section value range to be  from -90 to 90
}



void DistL_pid(double distance) {
  if (distance < threshold) {
    ultra_error = threshold - distance;
    Ser(ServoStraight + ultra_kpL * ultra_error);
    delay(10);
  }
}

void DistR_pid(double distance) {
  if (distance < threshold) {
    ultra_error = threshold - distance;
    Ser(ServoStraight - ultra_kpR * ultra_error);
    delay(10);
  }
}





void Sensor_disp() {
  Serial.print("  front:");
  Serial.print(front);
  Serial.print("  s_r:");
  Serial.print(servo_right);
  Serial.print("  right1:");
  Serial.print(right1);
  Serial.print("  right2:");
  Serial.print(right2);
  Serial.print("  back:");
  Serial.print(back);
  Serial.print(" left2:");
  Serial.print(left2);
  Serial.print("  left1:");
  Serial.print(left1);
  Serial.print("  s_l:");
  Serial.println(servo_left);
}


char read_cam()
{ int numg = 0;
  int numr = 0;
  int i;
  p.ccc.getBlocks();
  double a=(p.ccc.blocks[0].m_height)*(p.ccc.blocks[0].m_width);
  for (i = 0; i < p.ccc.numBlocks; i++)//this loop allows pixy cam to read
  {
    if (p.ccc.blocks[i].m_signature == 1)
    {
      numg++;
    }
    if (p.ccc.blocks[i].m_signature == 2 || p.ccc.blocks[i].m_signature == 3 || p.ccc.blocks[i].m_signature == 4)
    {
      numr++;
    }
  }
  if (numg >= 1 && a>=250) 
  {
    return('g');//when pixy cam see green pillar
  }
  else if (numr >= 1 && a>=250)
  {
    return('r');//when pixy cam see red pillar
  }
  else
  {
    return('n');//when pixy cam didn't see any thing
  }}
